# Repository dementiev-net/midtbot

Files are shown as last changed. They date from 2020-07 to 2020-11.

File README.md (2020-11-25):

MidTBot на ESP32
================

Простой перьевой плоттер на прошивке GRBL и плате ESP32. Этот репозиторий является выжимкой по сборке и настройке. Почитать подробнее можно на [тут](https://github.com/bdring/midTbot_esp32).

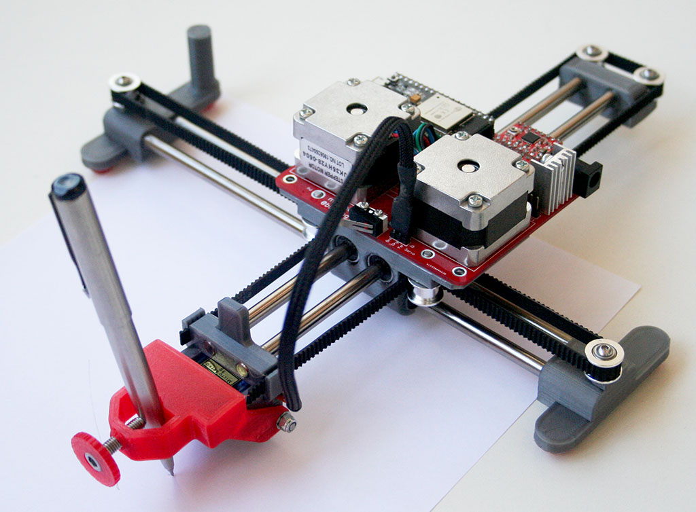
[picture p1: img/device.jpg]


## BOM:

###### PCB

|Name|Desc|Qty
|---|---|---
|C1,C2|Capacitor, Electrolytic 47uF 35V|2
|C3,C4|Capacitor MLCC 10uF 50V|2
|J1|DC Barrel Jack|1
|J2,J4|Header Male 1x4|2
|J3|Micro SD Socket TF-01A|1
|J5,J6|Header Male 1x3|2
|PS1|5VDC 1A Power Supply|1
|S1,S2|Microswitch Switch|2
|U1,U2|Header, Feamle 1x8|4
|U3|Header Female 1x19 (FYI: trimming a 1x20 works)|2
||**Required Modules**|
||StepStick A4988|2
||ESP32 Dev Kit (0.9" Wide Type)|1

###### Mechanical Parts List

|Name|Qty
|---|---
|Linear Bearing Shaft 6mm Dia. x 200 lg.|4
|Linear Bearing LM6LUU (wide Style)|4
|Pulley GT2 16Tooth 6mm 5mm Shaft|2
|Smooth Idler Pulley 3mm I.D. 16Tooth Dia 13mm Flange Dia|6
|Stepper Motor NEMA14 x 20mm Tall 5mm Shaft|2
|GT2 6mm Wide Belt|1m
|Button Screw M3 x 50mm|1
|Hex Nut M3 Locking|1
|Socket Head Screw M5 x 14|1
|Socket Head Screw M3 x 16|6
|Button Head Screw M3 x 8mm|6
|Bearing 3mm x 7mm x 3mm (683ZZ)|2
|Hobby Servo MG90S|1

## Прошивка в Arduino IDE

- При первой заливке скетча Grbl_Esp32 в ESP32 убедитесь, что он не вставлен в плату плоттера!
- В терминале Mac OS устанавливаем поддержку плат ESP32 (в репозитории автора есть информация для установки на другие операционные системы):

  ```
  mkdir -p ~/Documents/Arduino/hardware/espressif && \
  cd ~/Documents/Arduino/hardware/espressif && \
  git clone https://github.com/espressif/arduino-esp32.git esp32 && \
  cd esp32 && \
  git submodule update --init --recursive && \
  cd tools && \
  python get.py 
  ```
- Выбираем плату **ESP32 Dev Module** и схему **Minimal SPIFFS (1.9MB APP с OTA / 190KB SPIFFS)** в меню "Инструменты":

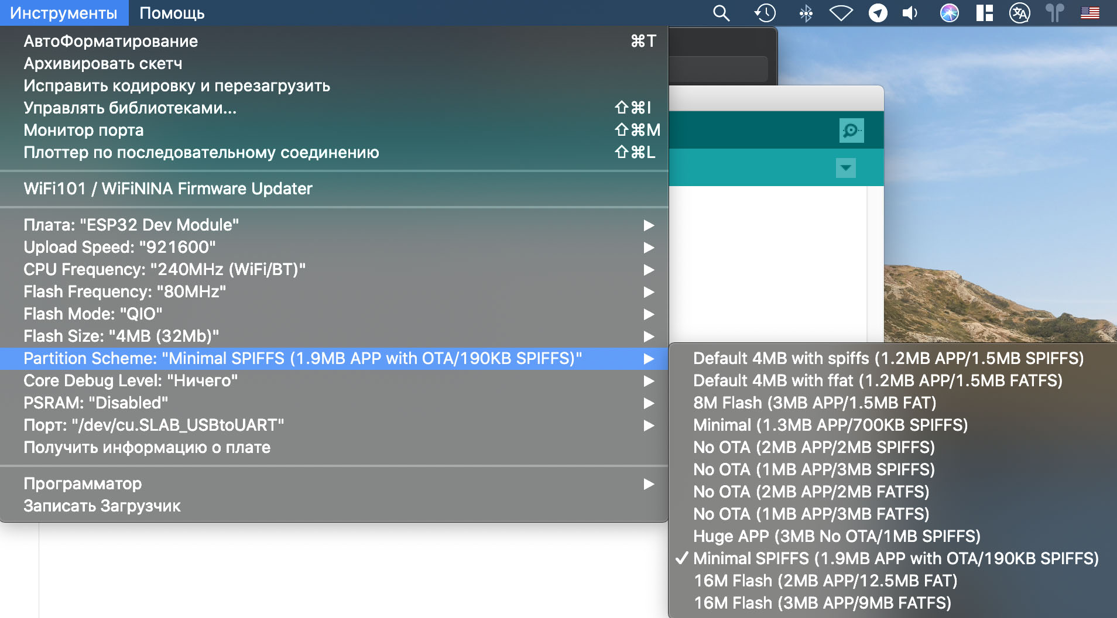
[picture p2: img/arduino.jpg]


- Компилируем **Grbl\_Esp32/Grbl\_Esp32.ino**
- Загружаем. При появлении ```Connecting........``` нужно удерживать кнопку "BOOT" на плате ESP32. При нормальной загрузке должно быть: ```Leaving... Hard resetting via RTS pin...```
- Проверяем настройки в "Мониторе порта". Нажимаем RESET на плате и видим:

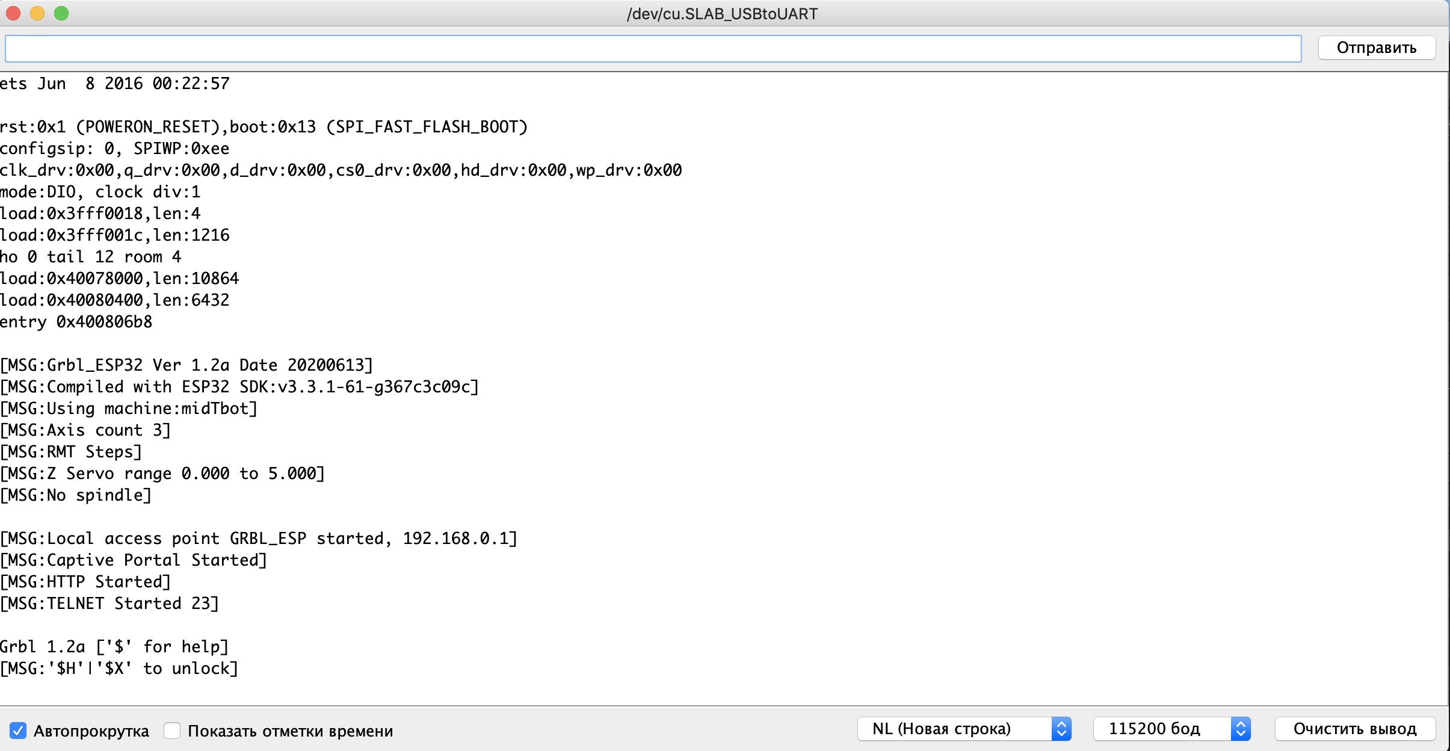
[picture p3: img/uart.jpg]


## Настройка моторов

- MidTbot использует механику CoreXY (всегда задействованы оба мотора). Если ось движется в неправильном направлении, то ставим настройку для X и Y ```$3 = 4``` или ```$3 = 0``` или разворачиваем разъем на 180 градусов
- Сбрасываем по умолчанию ```$rst = $```
- Проверка направления моторов: ```G91 G0X2 G0Y2```
- Проверка на парковку: ```$H```
- Установка тока двигателя для мотора **JK35HY28-0504** (0,5A): 

A4988:

```
Vref = Current Limit * 8 * 0,100(RS) = 0,5 / 1,25 = 0,4V
```

DRV8825 (на 70%):

```
Vref = Imax / 2 = 0,7 * 0,5 / 2 = 0,18V
```

## Настройка Pen Servo

- По команде ```G0Z5``` сервопривод должен переместиться вверх и по ```G0Z0``` вниз (перо на бумаге). Сервопривод должен вращаться по часовой стрелке, чтобы поднять ручку, и против часовой стрелки, чтобы опустить ее
- Можно отрегулировать конечные точки, изменив значения ```$102``` (для Z0) и ```$132``` (для Z5). Значение по умолчанию для каждого - ```100```, что соответствует 100%. Настройка ```$102 = 110``` добавит 10%. Настройка ```$102 = 90``` вычтет 10%
- Команда ```G10L2P0Z-5``` через консоль установит Z5, когда Z равна 0 (делается один раз, сохраняется во флэш-память).

## WebUI (Wi-Fi)

При первом включении будет создана точка доступа Wi-Fi со следующими настройками:

- SSID: ```GRBL_ESP```
- Пароль: ```12345678```
- IP-адрес : ```192.168.0.1```

Нужно подключится и загрузить файл данных ```Grbl_Esp32/data/index.html.gz```, содержащий веб-интерфейс.

Если скомпилировали прошивку с помощью ```ENABLE_AUTHENTIFICATION``` в ```config.h```, WebUI будет иметь двух пользователей с именами "admin" и "user". Если входим как "admin/admin", то  можем изменить любой параметр. Если вы вошли как "user/user", можем взаимодействовать только с Grbl. (Имена пользователей и пароли можно настроить перед компиляцией, отредактировав config.h).

Далее в **WebUI** нужно настроить как Wi-Fi клиент, а не точка доступа.

## Bluetooth

Как настроить написано тут: https://github.com/bdring/Grbl_Esp32/wiki/Using-Bluetooth

## Создание G-Code

Есть довольно популярная программа **InkScape** с плагином для генерации G-Code, но я привык рисовать в **CorelDraw**.

| | Скрин
|---|---
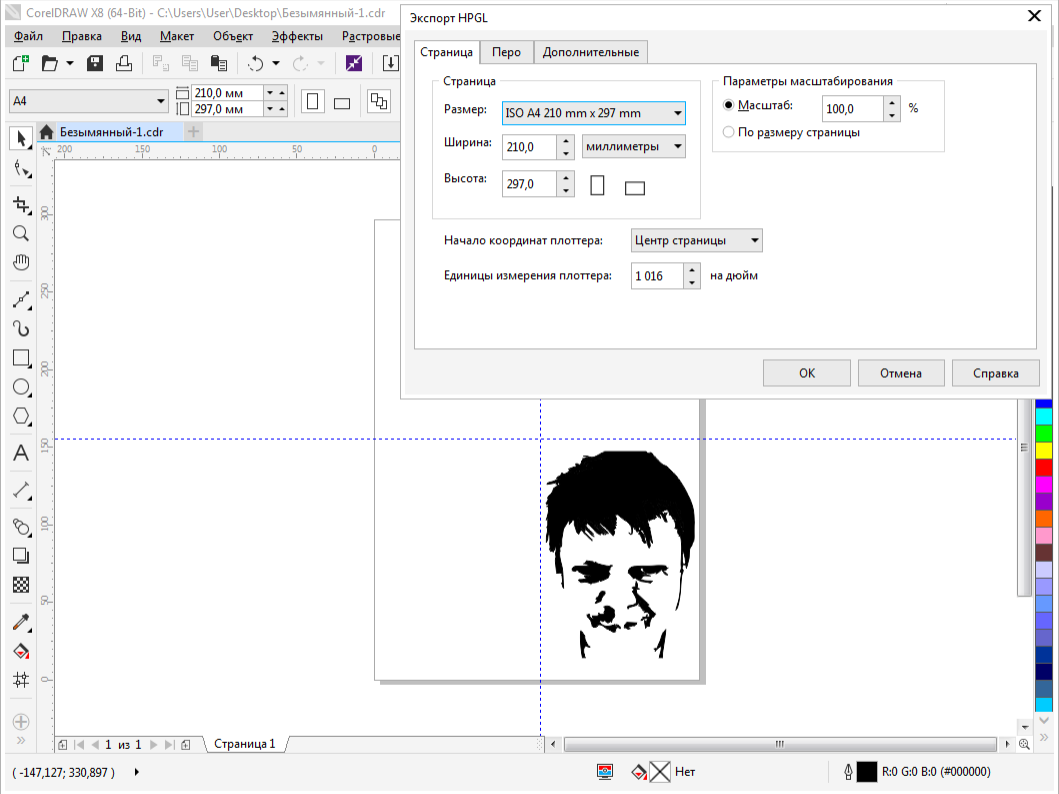
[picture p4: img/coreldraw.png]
| Рисуем в **CorelDraw** и экспортируем в HPGL. Для данного плоттера начало координат в центре страницы. От нее и располагаем рисунок | 
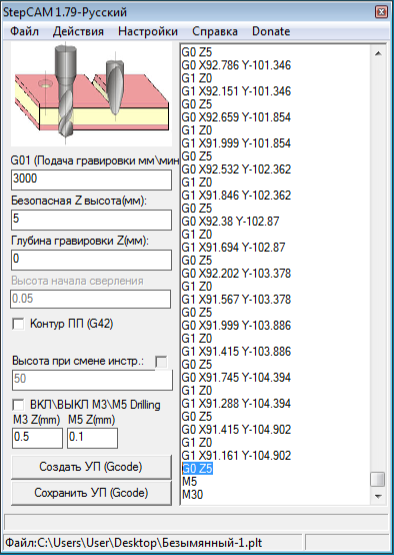
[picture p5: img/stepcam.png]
| С помощью программы **StepCAM** получаем G-Code. Не забываем добавить в конце коанду ```G0Z5``` для поднятия пера после завершения | 
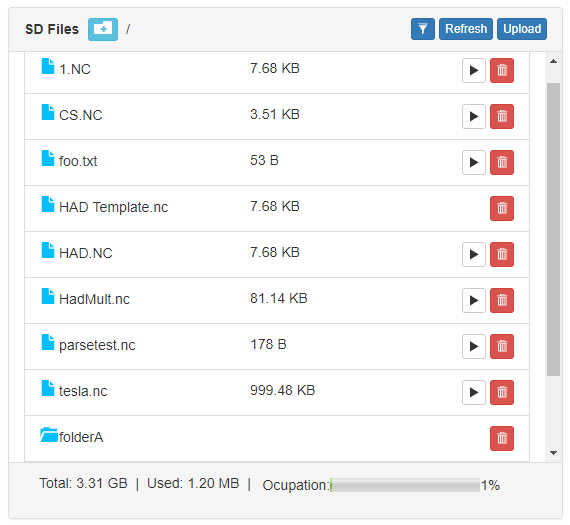
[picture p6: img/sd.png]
| Закидываем файл на карту памяти и в **WebUI** выбираем его для печати | 

## Контакты

GitHub автора: [https://github.com/bdring/midTbot_esp32](https://github.com/bdring/midTbot_esp32)

Grbl Esp32: [https://github.com/bdring/Grbl_Esp32](https://github.com/bdring/Grbl_Esp32)

Связаться со мной: info@dementiev.net

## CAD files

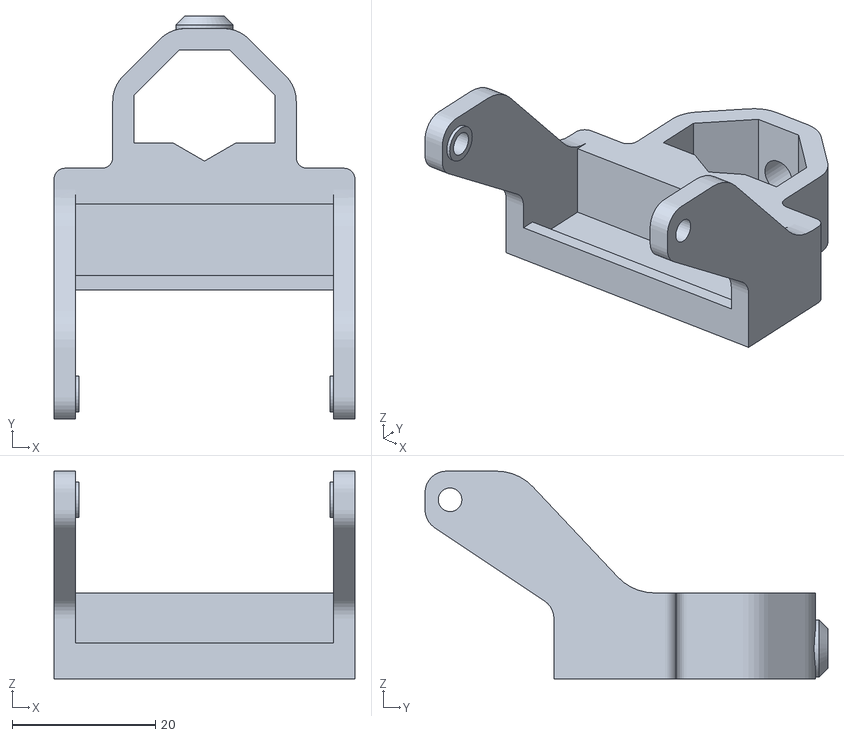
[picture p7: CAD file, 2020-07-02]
3d print/pen_mnt.stl
42.0 x 56.2 x 29.0

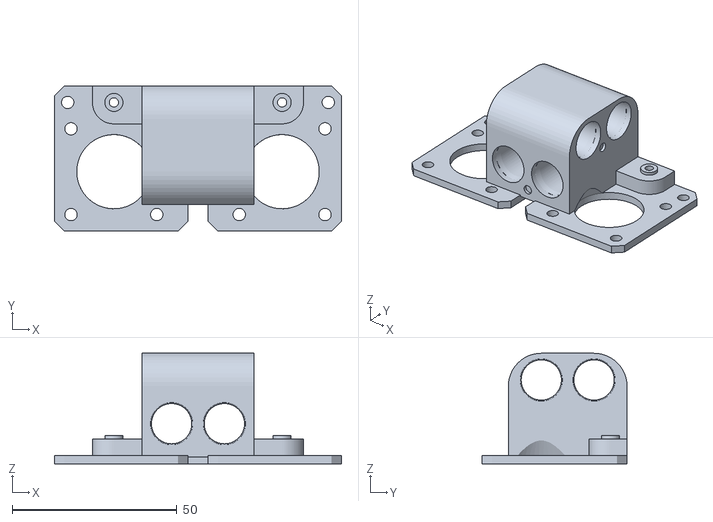
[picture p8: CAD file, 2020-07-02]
3d print/carriage_block.stl
87.0 x 44.0 x 33.5

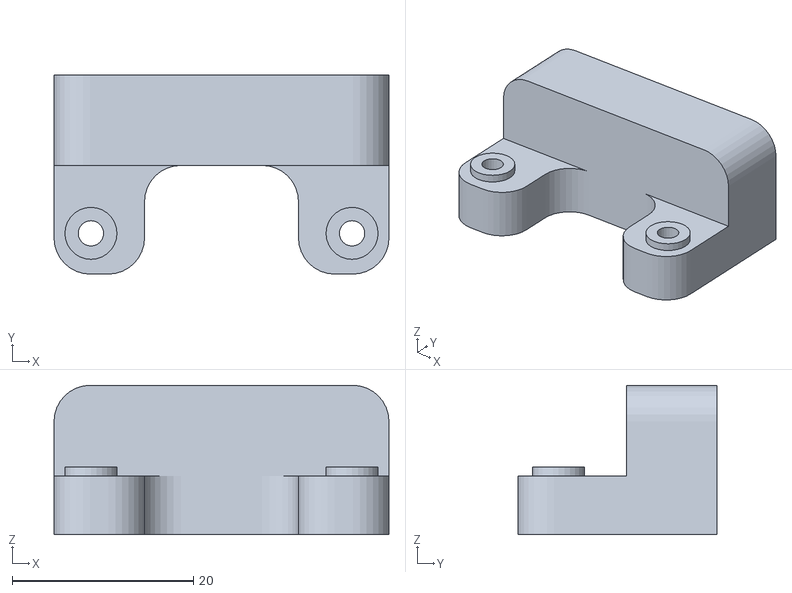
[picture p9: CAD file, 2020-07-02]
3d print/tailblock.stl
37.0 x 22.0 x 16.5

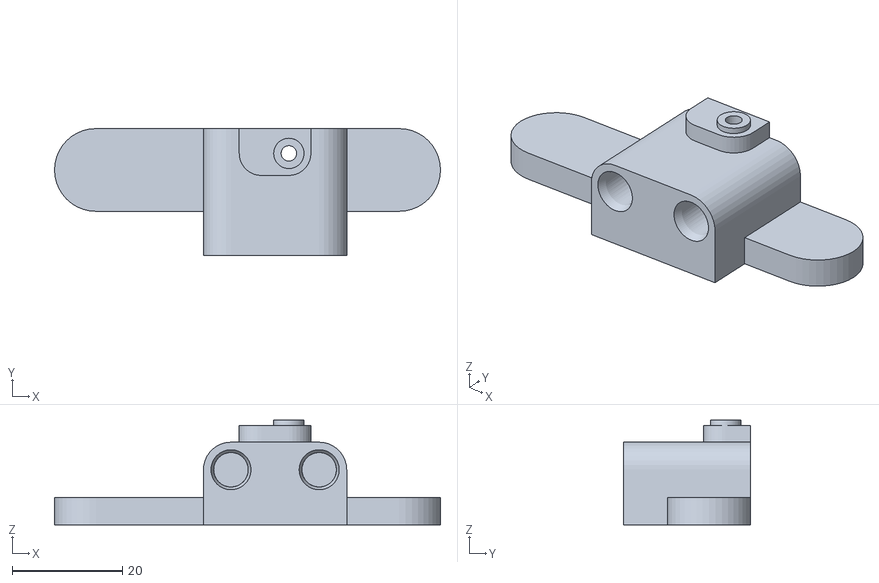
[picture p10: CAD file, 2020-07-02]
3d print/right_foot.stl
70.0 x 23.0 x 19.0

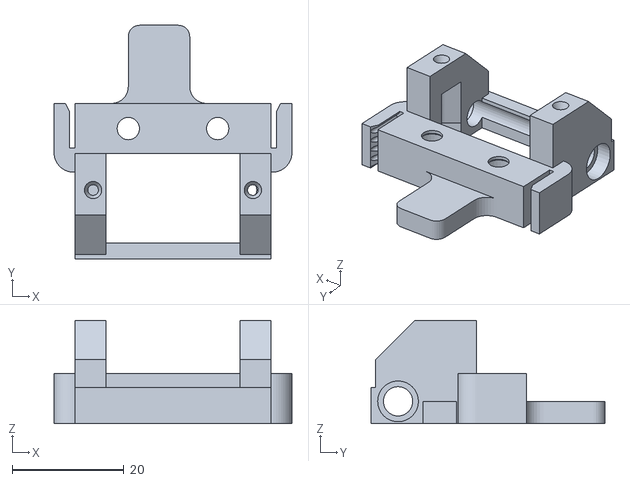
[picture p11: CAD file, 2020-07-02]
3d print/head_block_v2.stl
42.6 x 41.8 x 18.5

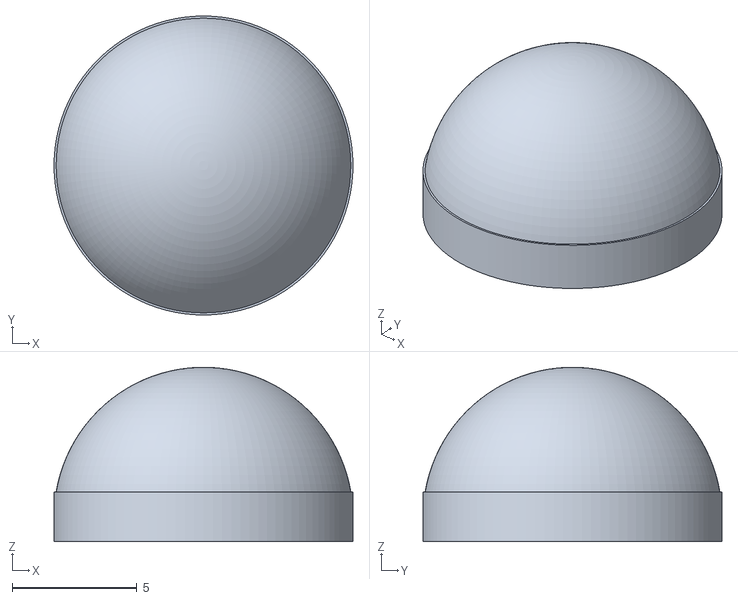
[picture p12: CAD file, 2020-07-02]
3d print/legs.stl
12.0 x 12.0 x 7.00

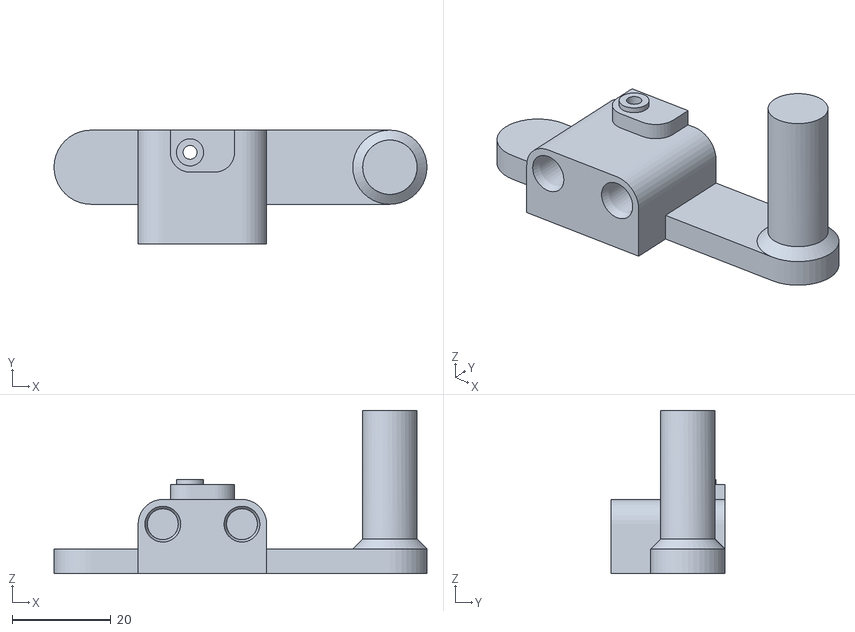
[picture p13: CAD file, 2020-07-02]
3d print/left_foot.stl
75.4 x 23.0 x 33.0

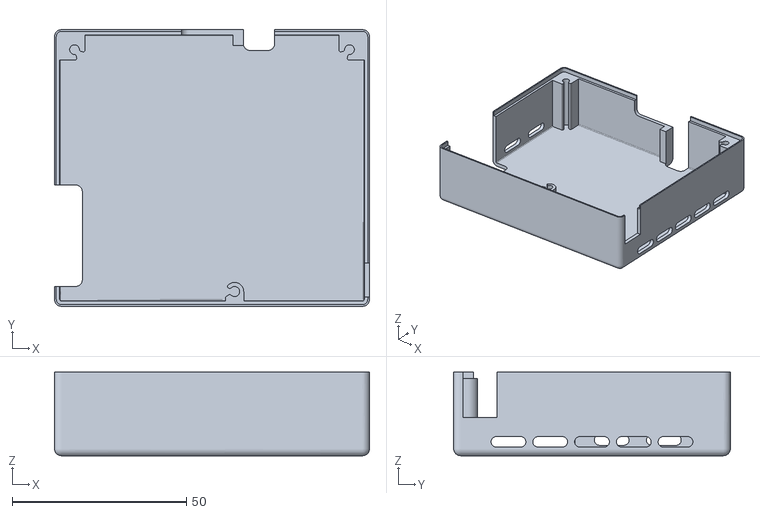
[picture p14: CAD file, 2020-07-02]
3d print/cover_v2.stl
90.5 x 79.5 x 24.0

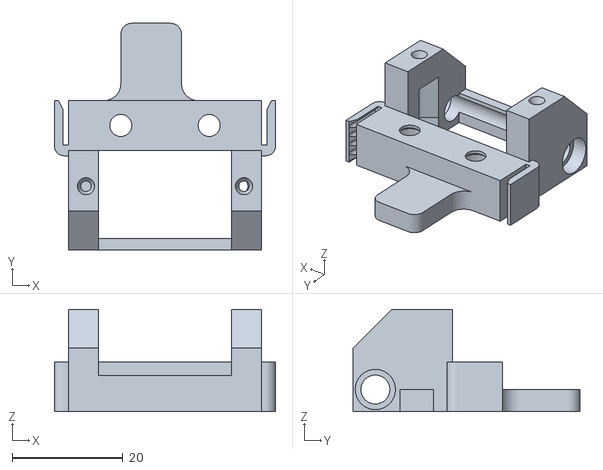
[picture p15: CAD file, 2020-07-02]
3d print/head_block.stl
40.0 x 41.0 x 18.5

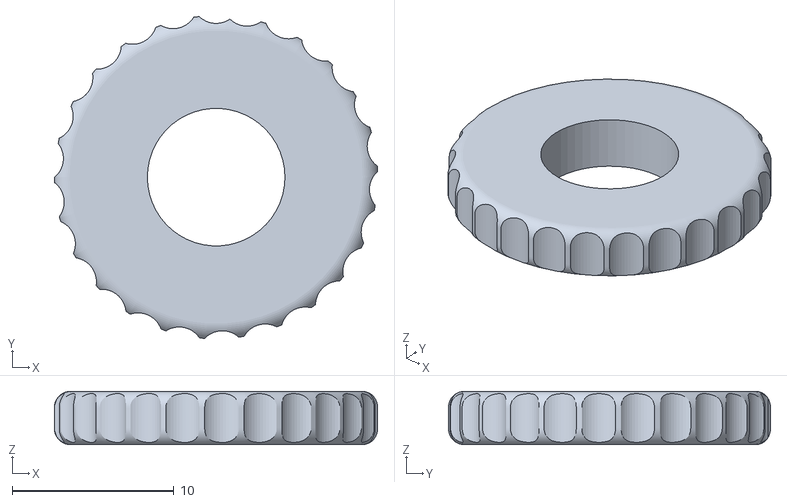
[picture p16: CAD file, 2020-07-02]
3d print/nut.stl
20.0 x 19.9 x 3.30

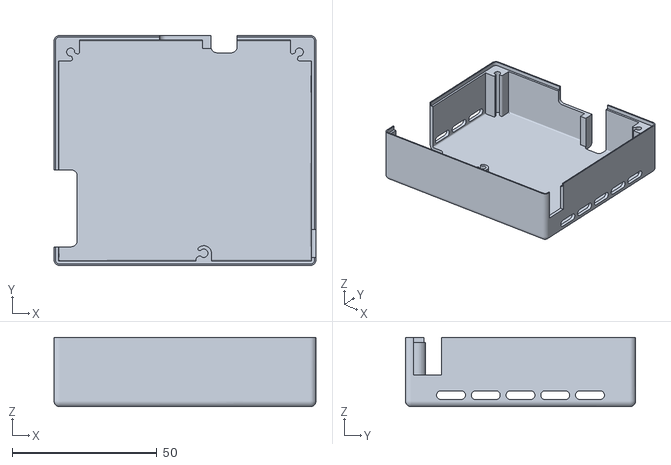
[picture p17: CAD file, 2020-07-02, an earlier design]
3d print/cover_v1.stl
90.5 x 79.5 x 24.0

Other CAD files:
3d print/carriage_block_v2.stl

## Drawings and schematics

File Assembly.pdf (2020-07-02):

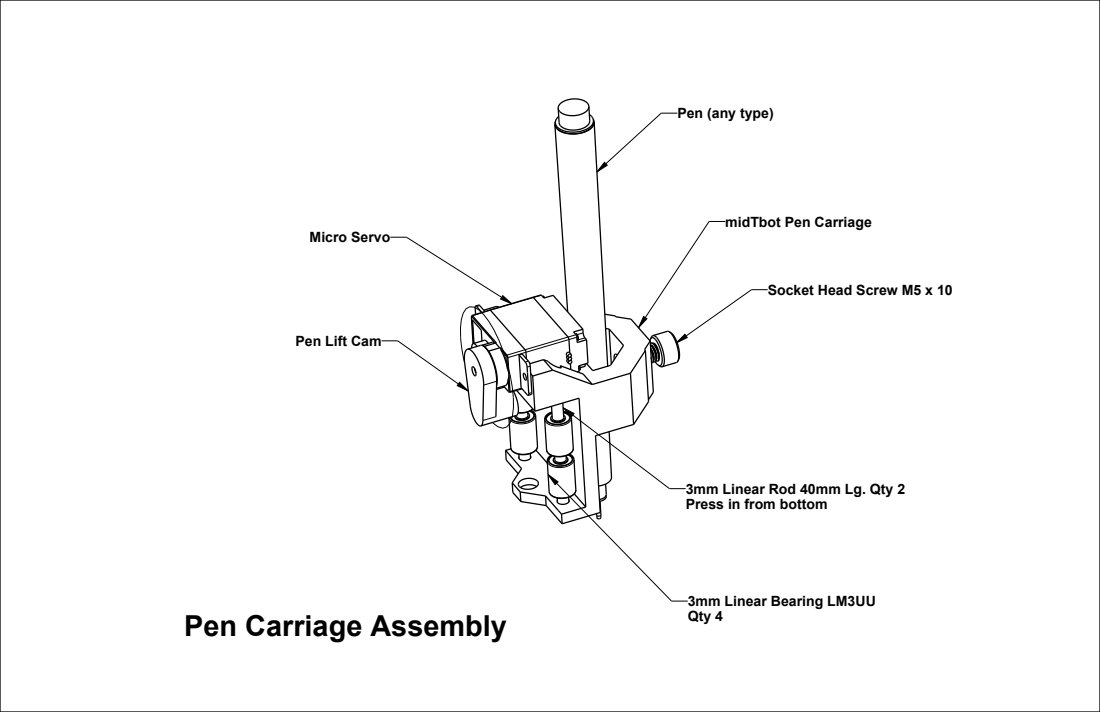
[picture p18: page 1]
Micro Servo; 3mm Linear Bearing LM3UU Qty 4

Pen (any type)

midTbot Pen Carriage

Socket Head Screw M5 x 10

Pen Lift Cam

3mm Linear Rod 40mm Lg. Qty 2
Press in from bottom

Pen Carriage Assembly

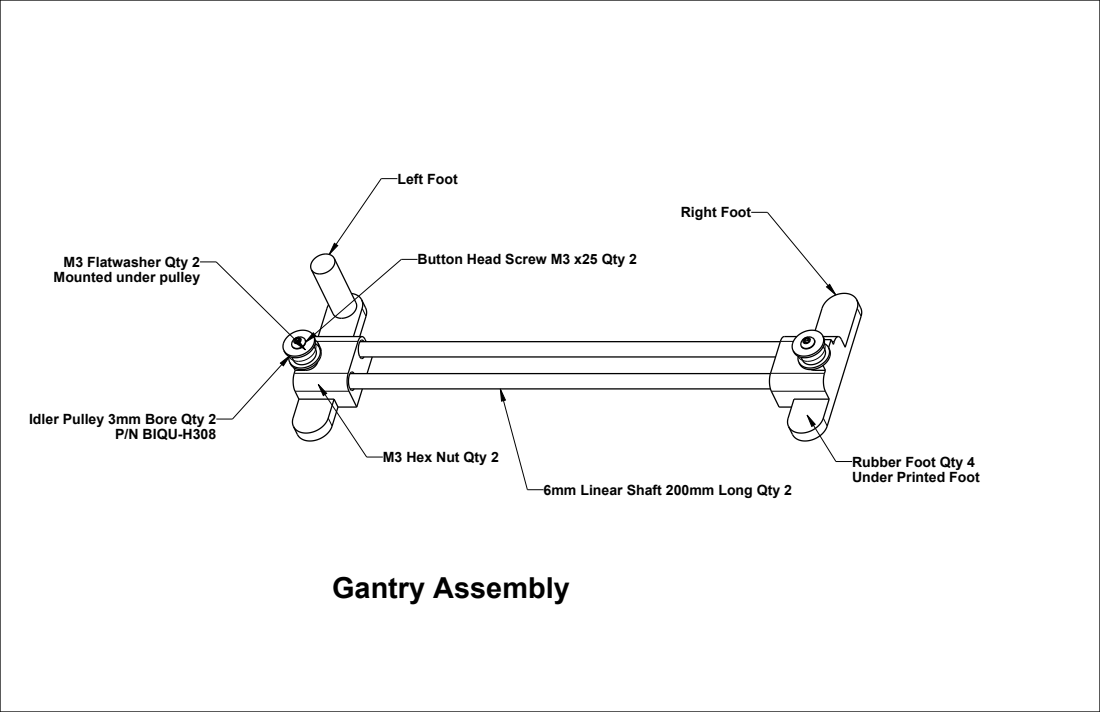
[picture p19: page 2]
Gantry Assembly; Right Foot; Left Foot; P/N BIQU-H308; M3 Hex Nut Qty 2; Rubber Foot Qty 4

M3 Flatwasher Qty 2
Mounted under pulley

Button Head Screw M3 x25 Qty 2

Idler Pulley 3mm Bore Qty 2

Under Printed Foot

6mm Linear Shaft 200mm Long Qty 2

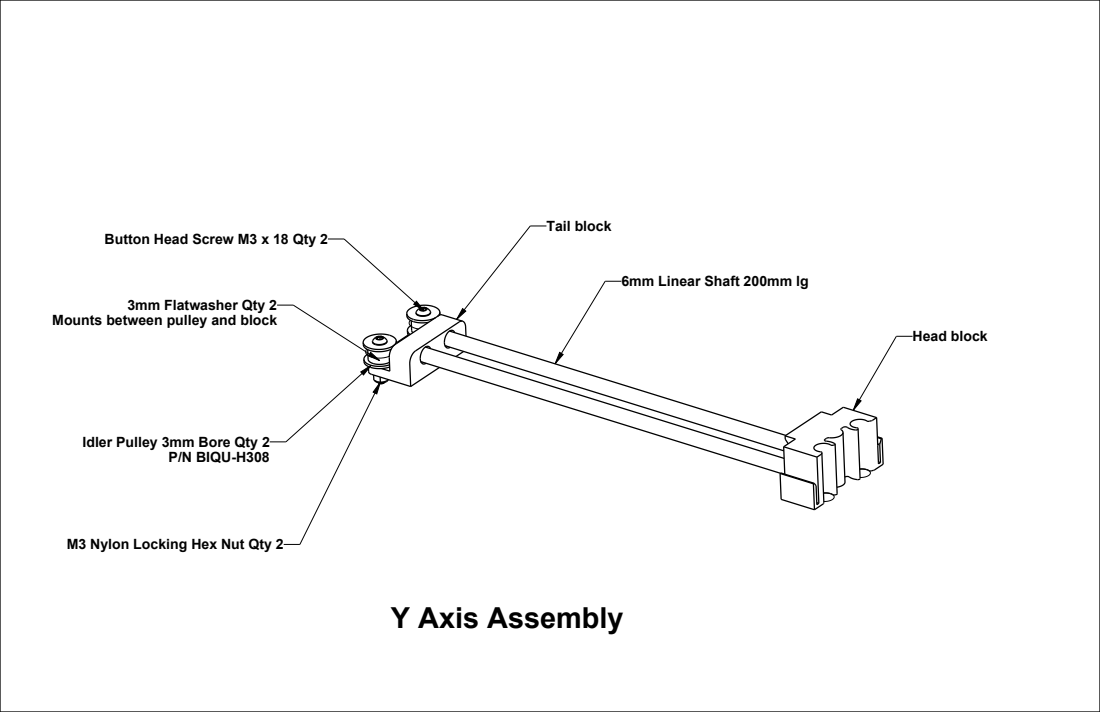
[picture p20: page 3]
Y Axis Assembly; Tail block; Head block; 3mm Flatwasher Qty 2; P/N BIQU-H308

Button Head Screw M3 x 18 Qty 2

6mm Linear Shaft 200mm lg

Mounts between pulley and block

Idler Pulley 3mm Bore Qty 2

M3 Nylon Locking Hex Nut Qty 2

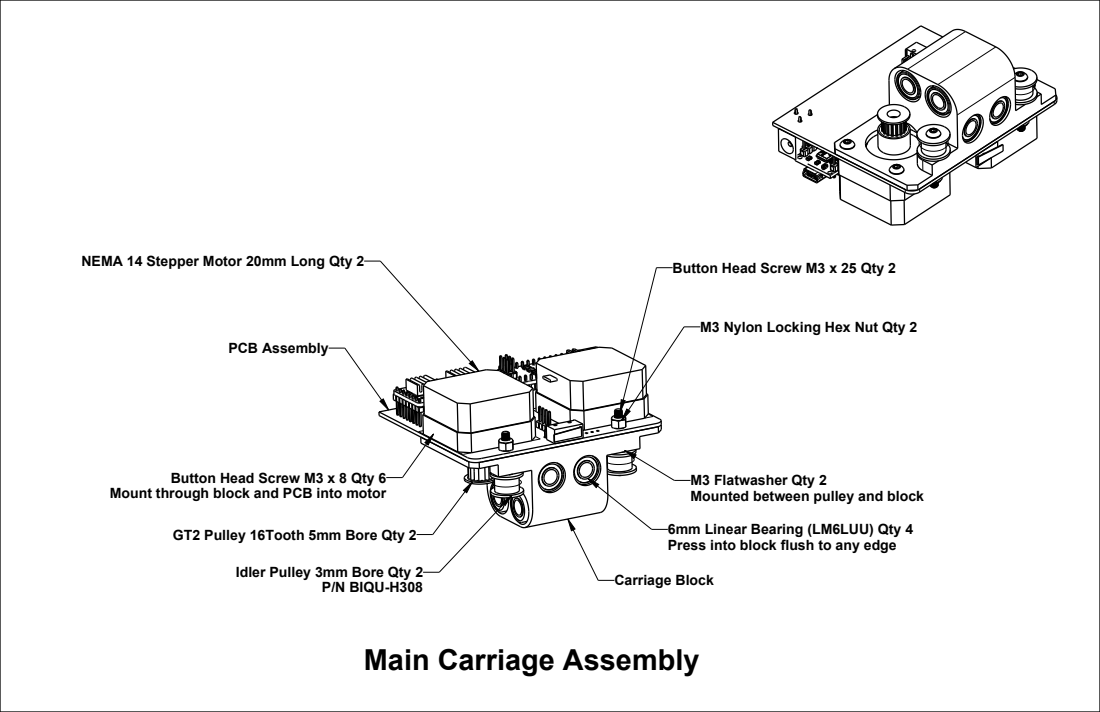
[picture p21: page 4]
PCB Assembly

Button Head Screw M3 x 25 Qty 2 NEMA 14 Stepper Motor 20mm Long Qty 2

M3 Nylon Locking Hex Nut Qty 2

Button Head Screw M3 x 8 Qty 6

M3 Flatwasher Qty 2
Mounted between pulley and block
6mm Linear Bearing (LM6LUU) Qty 4
Press into block flush to any edge
Carriage Block

Mount through block and PCB into motor

GT2 Pulley 16Tooth 5mm Bore Qty 2

Idler Pulley 3mm Bore Qty 2

P/N BIQU-H308
Main Carriage Assembly

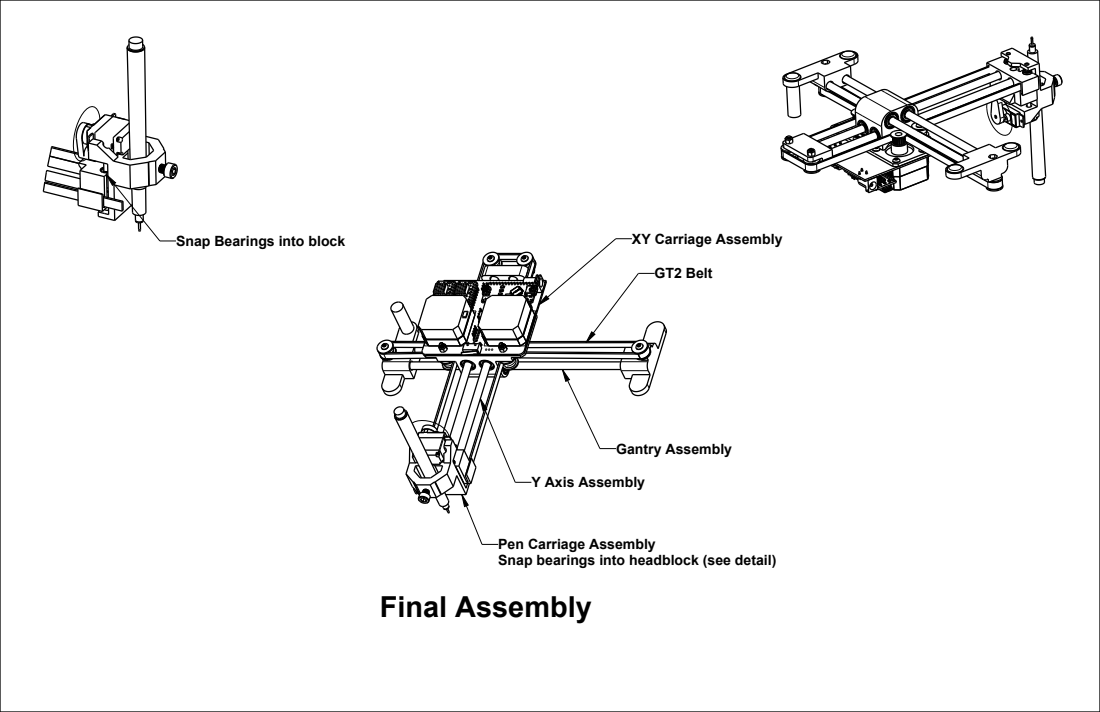
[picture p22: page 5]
Gantry Assembly; Y Axis Assembly; SCALE 0.666; Snap Bearings into block

XY Carriage Assembly
GT2 Belt

Pen Carriage Assembly
Snap bearings into headblock (see detail)
Final Assembly

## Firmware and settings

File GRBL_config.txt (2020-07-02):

$0=3
$1=255
$2=0
$3=4
$4=0
$5=1
$6=0
$10=1
$11=0.010
$12=0.002
$13=0
$20=0
$21=0
$22=1
$23=1
$24=200.000
$25=1000.000
$26=250
$27=3.000
$30=1000.000
$31=0.000
$32=0
$100=400.000
$101=200.000
$102=100.000
$110=5000.000
$111=5000.000
$112=3000.000
$120=200.000
$121=200.000
$122=100.000
$130=100.000
$131=100.000
$132=100.000

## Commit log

2020-07-02 Добавление файлов
    [GRBL_config.txt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]
2020-07-02 Правка README.md
2020-11-04 Поменял описание
2020-11-17 Повторная выгрузка на Github
    [GRBL_config.txt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]
2020-11-25 Правка описания
